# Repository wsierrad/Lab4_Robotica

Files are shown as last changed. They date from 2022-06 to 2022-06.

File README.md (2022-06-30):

# Lab 4 Robotica
## Integrantes:

Fabian Steven Galindo Peña  
Brian Alejandro Vásquez González  
William Arturo Sierra Díaz  

## Diseño de la herramienta.
Para el diseño de la herramienta se tuvieron en cuenta varios aspectos como
+ Dimensiones del marcador
+ Angulo de orientación de la herramienta
+ Maxima compresión del porta herramientas

Con esto claro se llegó a un diseño que contempla el uso de un resorte y se compone de dos partes hechas en PLA por medio de impresión 3D, el diseño detallado de estas piezas se puede ver en los [planos adjuntos al repo](Planos/)

A continuacion se detallan los planos finales del portaherramientas elaborado:  
Primero podemos observar la base que tiene un radio interno de 9.5mm para el acople del marcador, ademas se realizo una guia de 7x3mm cuadrada con la cual se buscaba que el marcador se deslizara unicamente en el eje z asi al marcador se le realizo una modificacion añadiendo las guías para el desplazamiento de este, adicionalmente vemos en la parte inferior el diseño para el acople con el portaherramientas del Robot que usa 4 tornillos M6 segun se describe en la hoja de especificaiones tecnicas de este.  
  
A continuacion se muestra el diseño de la tapa que contempla una seccion interna de 19mm de diametro para que la punta del marcador pueda pasar y asi realizar la escritura sobre la superficie deseada.  
  
Se eligio impresión 3D para un prototipado y rápida fabricacion, además de que por la aplicación no habáan grandes fuerzas que contemplar en la herramienta.   
De esta forma se logro fabricar tal como se ven en las siguiente imágenes  
   
Posteriormente se procedio a ensamblar como se detalla en la siguiente imágen  


## Código en RAPID del módulo utilizado para el desarrollo de la práctica.
Para comenzar con el desarrollo del lab se planteo usar workobjects desde el principio de esta forma se facilitaba el cambio este un plano a un plano inclinado a 30°  
Asi lo primero que tenemos en nuestra programación es la definición de la posición y orientación de cada WorkObject que se guardan en las variables tipo wobjdata con nombres Cuadrante1 y Cuadrante2. 
Luego en la tercera línea del módulo se encuentra la posición y orientación de nuestra herramienta, definida por la calibración como se explica en la siguiente sección donde se podra ver el procedimiento realizado más a fondo.
```
MODULE ModuleFab
    PERS wobjdata Cuadrante1:=[FALSE,TRUE,"",[[200,600,10],[1,0,0,0]],[[0,0,0],[1,0,0,0]]];
    PERS wobjdata Cuadrante2:=[FALSE,TRUE,"",[[450,-400,110],[0.683012702,-0.183012702,-0.183012702,-0.683012702]],[[0,0,0],[1,0,0,0]]];
    PERS tooldata Marker:=[TRUE,[[-0.917808,-1.75486,202.667],[0.812949,-0.58005,0.0419499,-0.0299318]],[0.2,[0,0,1],[1,0,0,0],0,0,0]];
```
Posterior a esto vemos la definición de constantes, estos van a ser los puntos guía para nuestra trayectoria, para ver todo el código completo puede consultar el programa [adjunto al repo](ModuleFab.mod)
```
    CONST robtarget Target_5:=[[-54.660161362,322.568528773,705.32582312],[0.5,-0.683012702,-0.5,-0.183012702],[0,0,0,0],[9E+09,9E+09,9E+09,9E+09,9E+09,9E+09]];
    CONST robtarget Target_10:=[[0.000029436,0.000002786,-0.00001954],[0,1,0,0],[0,0,0,0],[9E+09,9E+09,9E+09,9E+09,9E+09,9E+09]];
    CONST robtarget Target_20:=[[85.00007128,0.000056558,-0.000067404],[0.000000052,1,0.00000008,0.000000048],[0,-1,0,0],[9E+09,9E+09,9E+09,9E+09,9E+09,9E+09]];
    CONST robtarget Target_30:=[[100,-40,0],[0,1,0,0],[0,0,0,0],[9E+09,9E+09,9E+09,9E+09,9E+09,9E+09]];
    .
    .
    .
    CONST robtarget Target_230:=[[100.00010508,-280.000701552,-0.002614694],[-0.000000019,1,-0.000000044,0.000000209],[0,-1,0,0],[9E+09,9E+09,9E+09,9E+09,9E+09,9E+09]];
    CONST robtarget Target_240:=[[100.000114302,-280.00069038,19.997361362],[-0.000000031,1,-0.000000041,0.000000218],[0,-1,0,0],[9E+09,9E+09,9E+09,9E+09,9E+09,9E+09]];
    CONST robtarget Target_250:=[[0.000008509,0.000003577,-0.00001118],[0.000000006,1,0,-0.000000002],[0,0,0,0],[9E+09,9E+09,9E+09,9E+09,9E+09,9E+09]];
    CONST robtarget Target_260:=[[-54.660161362,322.568528773,705.32582312],[0.5,-0.683012702,-0.5,-0.183012702],[0,0,0,0],[9E+09,9E+09,9E+09,9E+09,9E+09,9E+09]];
```
Posterior a esto se definio el main el cual ejecutara dos procedimientos ya declarados que contendrán las isntrucciones para moverse en cada workObject
```
    PROC main10()
        Path_10;
        Path_20;
    ENDPROC
```
Por ultimo en cada procedimiento se declararon las instrucciones MOVL necesarias para realizar la trayectoria deseada siguiendo todos los puntos previamente definidos, en cada instrucción se definía la velocidad la cual es estandar para todos los movimiento y se estableció en 200 mm/s y el valor de Z en 10 para lograr realizar los trazos  
Para este procedimiento podemos ver que tenemos dos puntos que hacen referencia al Cuadrante2 esto es porque se seleccionó como Home el Home del Robot y se estableció este Home respecto a el segundo workObject.  
```
PROC Path_10()
        MoveL Target_5,v200,z10,Marker\WObj:=Cuadrante2;
        MoveL Target_10,v200,z10,Marker\WObj:=Cuadrante1;
        MoveL Target_20,v200,z10,Marker\WObj:=Cuadrante1;
        MoveL Target_30,v200,z10,Marker\WObj:=Cuadrante1;
        MoveL Target_40,v200,z10,Marker\WObj:=Cuadrante1;
        MoveL Target_50,v200,z10,Marker\WObj:=Cuadrante1;
        MoveL Target_60,v200,z10,Marker\WObj:=Cuadrante1;
        MoveL Target_70,v200,z10,Marker\WObj:=Cuadrante1;
        MoveL Target_75,v200,z10,Marker\WObj:=Cuadrante1;
        .
        .
        .
        MoveL Target_190,v200,z10,Marker\WObj:=Cuadrante1;
        MoveL Target_200,v200,z10,Marker\WObj:=Cuadrante1;
        MoveL Target_210,v200,z10,Marker\WObj:=Cuadrante1;
        MoveL Target_220,v200,z10,Marker\WObj:=Cuadrante1;
        MoveL Target_230,v200,z10,Marker\WObj:=Cuadrante1;
        MoveL Target_240,v200,z10,Marker\WObj:=Cuadrante1;
        MoveL Target_250,v200,z10,Marker\WObj:=Cuadrante1;
        MoveL Target_260,v200,z10,Marker\WObj:=Cuadrante2;
    ENDPROC
```
Y asi se definió tambien para el Path_20 que contiene las instrucciones para el movimiento en el plano inclinado
```
    PROC Path_20()
        MoveL Target_5,v200,z10,Marker\WObj:=Cuadrante2;
        MoveL Target_10,v200,z10,Marker\WObj:=Cuadrante2;
        MoveL Target_20,v200,z10,Marker\WObj:=Cuadrante2;
        MoveL Target_30,v200,z10,Marker\WObj:=Cuadrante2;
        MoveL Target_40,v200,z10,Marker\WObj:=Cuadrante2;
        MoveL Target_50,v200,z10,Marker\WObj:=Cuadrante2;
        MoveL Target_60,v200,z10,Marker\WObj:=Cuadrante2;
        MoveL Target_70,v200,z10,Marker\WObj:=Cuadrante2;
        .
        .
        .
        MoveL Target_180,v200,z10,Marker\WObj:=Cuadrante2;
        MoveL Target_190,v200,z10,Marker\WObj:=Cuadrante2;
        MoveL Target_200,v200,z10,Marker\WObj:=Cuadrante2;
        MoveL Target_210,v200,z10,Marker\WObj:=Cuadrante2;
        MoveL Target_220,v200,z10,Marker\WObj:=Cuadrante2;
        MoveL Target_230,v200,z10,Marker\WObj:=Cuadrante2;
        MoveL Target_240,v200,z10,Marker\WObj:=Cuadrante2;
        MoveL Target_250,v200,z10,Marker\WObj:=Cuadrante2;
        MoveL Target_260,v200,z10,Marker\WObj:=Cuadrante2;
    ENDPROC
```
De esta forma se completó el desarrollo del código y se procedió a realizar las pruebas en el laboratorio despues de haber realizado la simulación en RobotStudio
## Calibración de la herramienta

Ya construida la herramienta se procede a ensamblar el portaherramienta, y se procede a realizar la calibración. A partir del ensamble en el espacio de trabajo de un punto fijo para tener un punto de referencia y utilizar el método de acercamiento en el eje z y acercamiento de la herramienta por 3 diferentes configuraciones del robot. Se realizo una primera calibración como se ve en la imagen de la definición de la herramienta, aquí se observa que el error máximo es de 2,4 mm, error mínimo de 2,2 mm y un error promedio de 2,3 mm. Estos errores se podrían compensar con la distancia de retracción que aporta el resorte de la herramienta sin embargo se toma la decisión de repetir la calibración. De la cual el grupo de trabajo olvido tomar foto, pero su error promedio era alrededor de 0,5 mm. 

  
  

## Simulación en RobotStudio
A continuacion se puede ver la simulación final en RobotStudio en la cual el Robot realiza las dos trayectorias cumpliendo los requerimientos de la práctica  
Practica 4: Simulación (https://youtu.be/zRVmG34LNds)
## Implementación de la práctica con los robots reales.
A continuacion se puede ver la implementacion con el robot en el laboratorio LabSir en la cual el Robot realiza las dos trayectorias cumpliendo los requerimientos de la practica.  
Practica 4: Implementación Real (https://youtu.be/nFzFDuL_ORQ)

## Descripción de la solución planteada
Se describe la solución planteada:
-	En primer lugar, se diseña la herramienta, se desea usar una herramienta con resorte para darle algo de tolerancia al marcador. Se genera su diseño CAD, y se imprime en 3D, para luego ser ensamblada en el robot.
-	Esta herramienta en modelo CAD, se importa a RobotStudio, para realizar su calibración en el software. 
-	Se realiza la calibración de la herramienta, y este resultado se compara con el de RobotStudio, para verificar diferencias en distancias entre la simulación y el mundo real, tras la pieza ser implementada.
-	En el software, se crean los dos workobjects, para cada una de las escrituras, y así facilitar su desplazamiento de ser necesario.
-	Se diseña la trayectoria que debe realizar el robot, para trazar las iniciales de los tres integrantes Brian (B), Fabian (F) y William (W). Se programaron todos los robtargets, que posteriormente generan los paths. Estos paths se sincronizan con RAPID para generar el módulo, que será importado posteriormente al robot. Se tuvieron en cuenta todas las indicaciones del laboratorio, a la hora de crear estas trayectorias.
-	Se importa el módulo al controlador, y se realizan los trazos. Se verifican las distancias, y se cuadran las posiciones de los workobjects, para que todo este correcto, y así lograr las tareas deseadas.

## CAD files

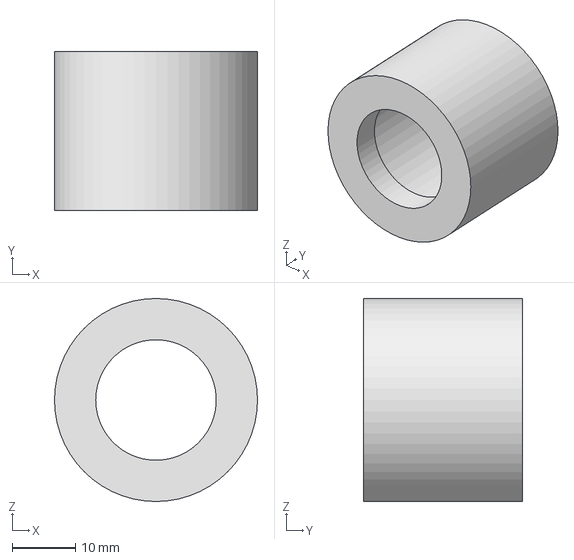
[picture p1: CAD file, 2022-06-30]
Piezas/Step/Tapastep.stp
32.0 x 25.0 x 32.0 mm

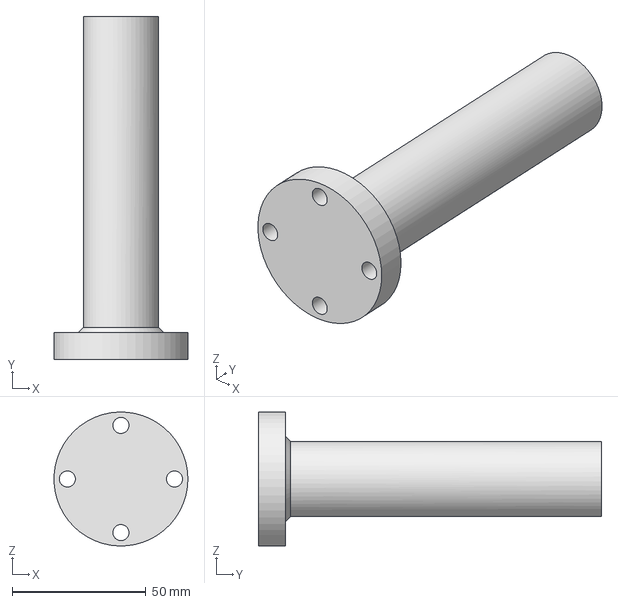
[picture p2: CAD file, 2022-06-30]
Piezas/Step/Basestep.stp
50.0 x 128.0 x 50.0 mm

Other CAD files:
Planos/Basestep.dwg
Planos/Tapastep.dwg
Piezas/Basestep.ipt
Piezas/Tapastep.ipt

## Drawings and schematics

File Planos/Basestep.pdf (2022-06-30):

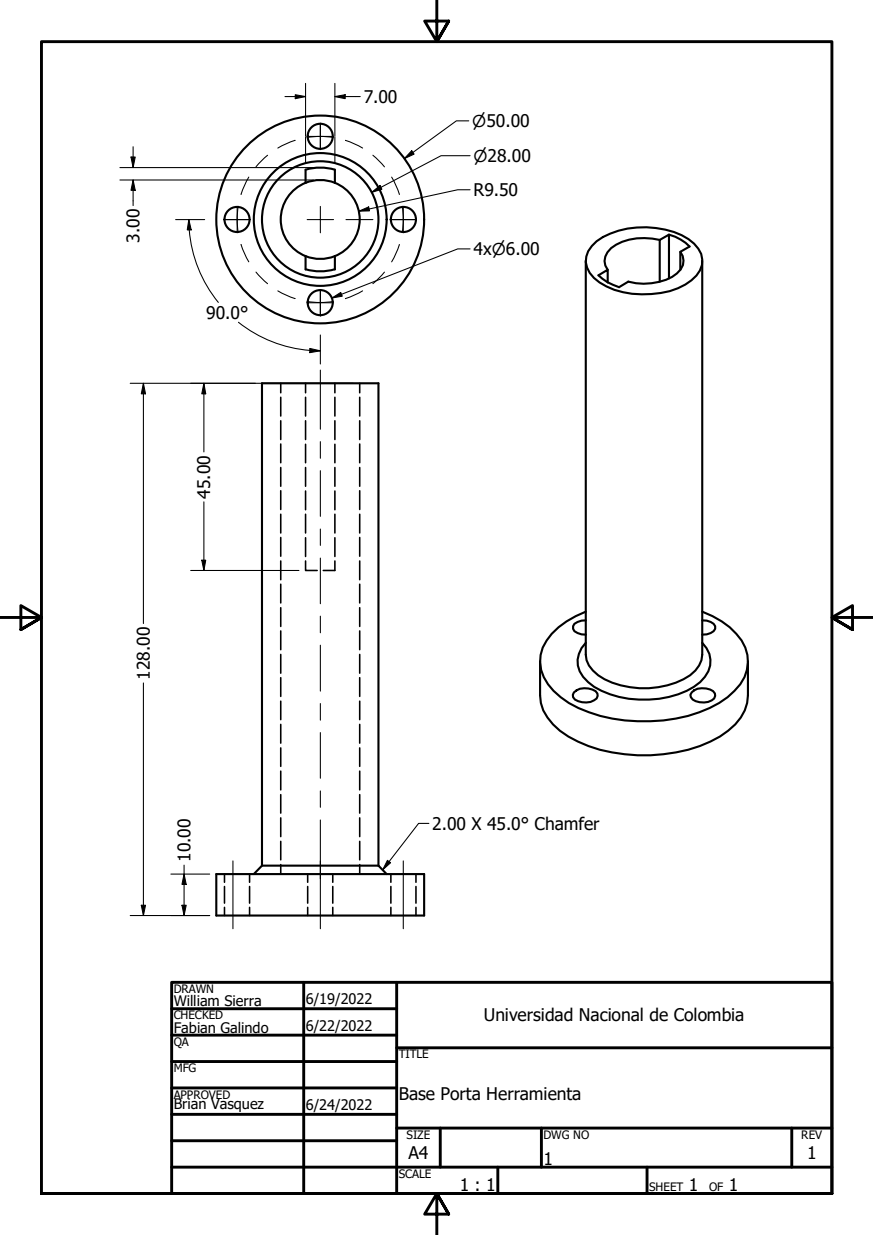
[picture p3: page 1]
2.00 X 45.0° Chamfer

DRAWN William Sierra | 6/19/2022 | Universidad Nacional de Colombia

CHECKED Fabian Galindo | 6/22/2022

MFG

APPROVED Brian Vasquez | 6/24/2022

Base Porta Herramienta

SIZE A4 | DWG NO 1 | REV 1

SCALE 1 : 1 | | SHEET 1 OF 1

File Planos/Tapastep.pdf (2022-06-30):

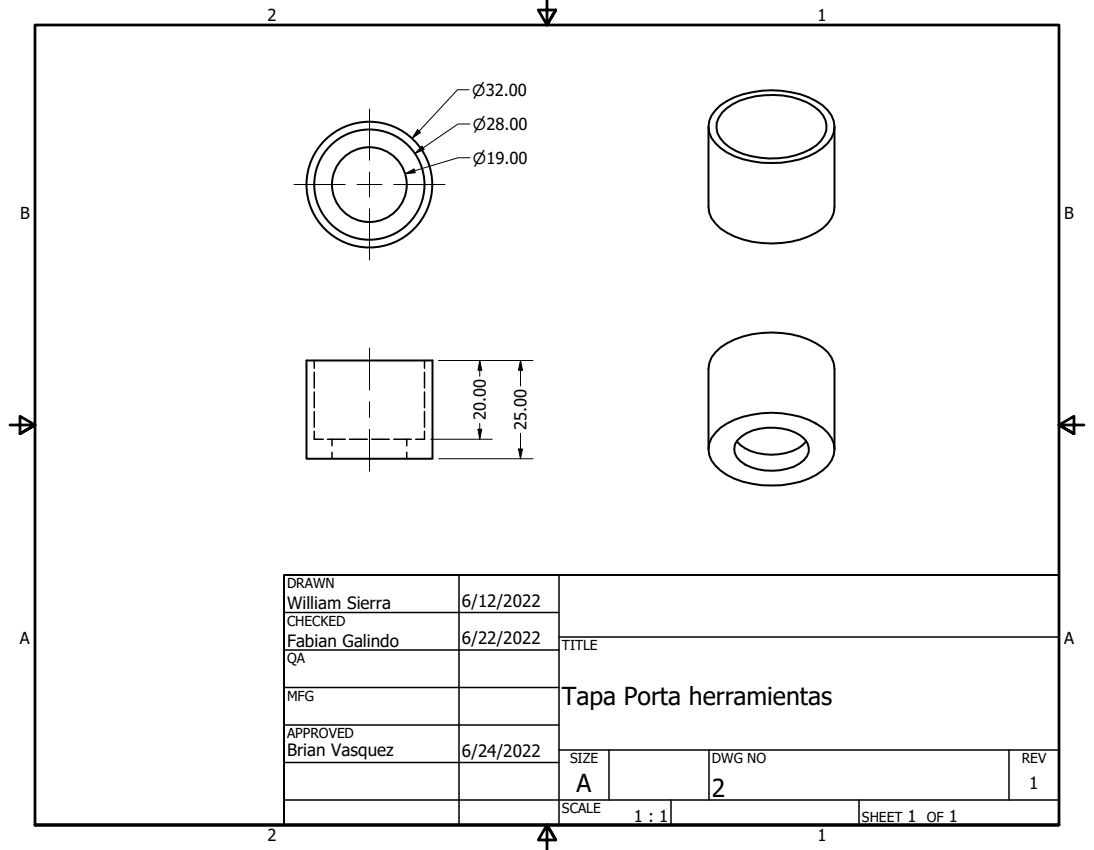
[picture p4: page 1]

DRAWN William Sierra | 6/12/2022

CHECKED Fabian Galindo | 6/22/2022

MFG

Tapa Porta herramientas

APPROVED Brian Vasquez | 6/24/2022

SIZE A | DWG NO 2 | REV 1

SCALE 1 : 1 | | SHEET 1 OF 1
